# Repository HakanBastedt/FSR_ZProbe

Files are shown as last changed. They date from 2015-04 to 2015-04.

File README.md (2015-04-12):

# FSR_ZProbe
My take on FSR Z-Probe for Marlin and Repetier

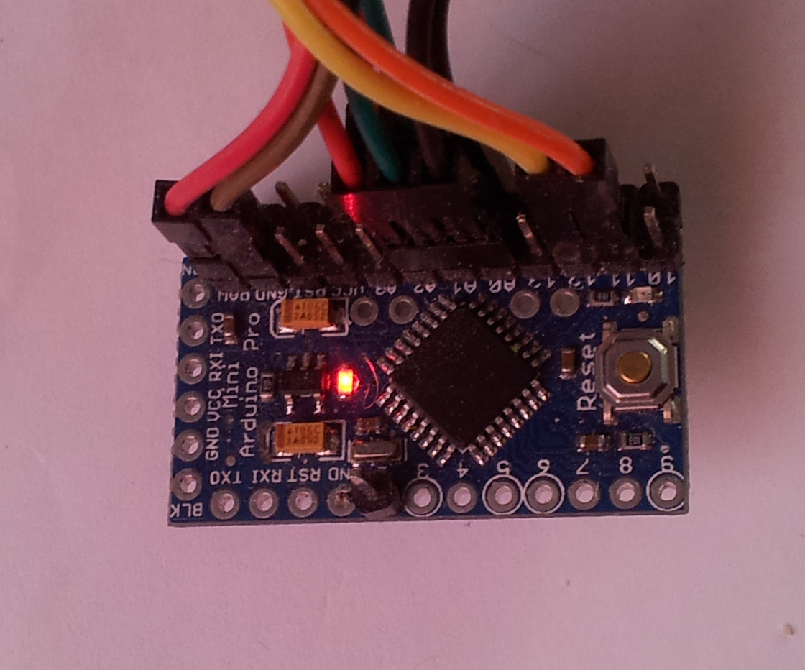
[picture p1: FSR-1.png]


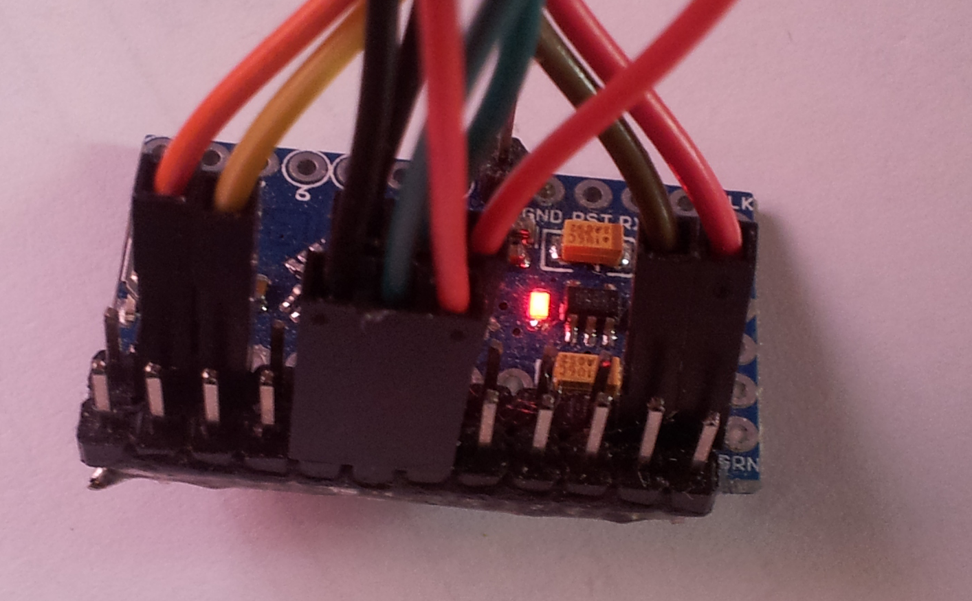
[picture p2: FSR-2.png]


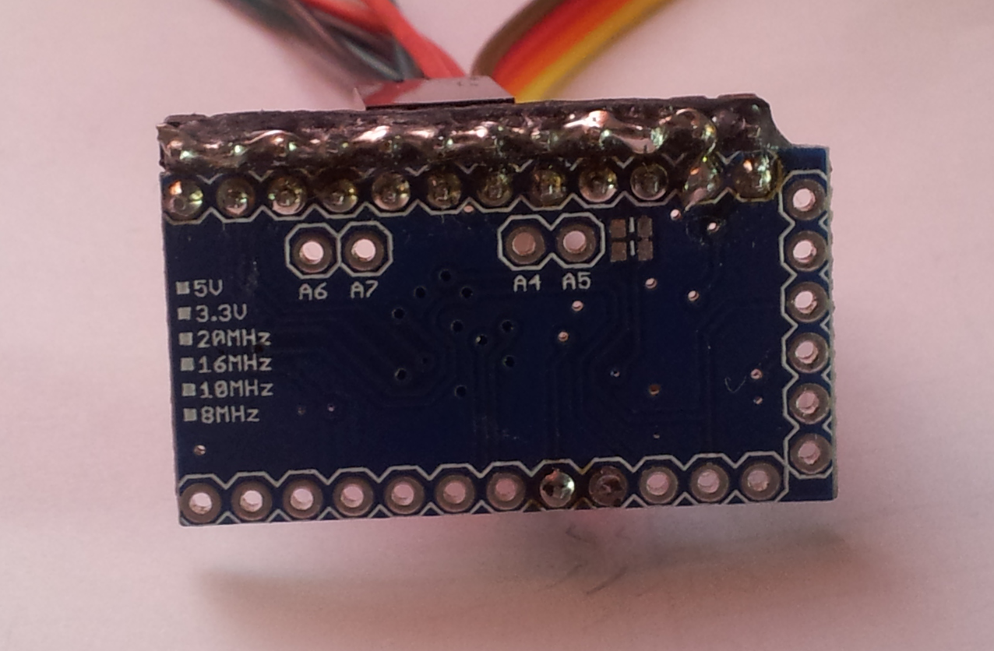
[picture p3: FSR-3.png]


For Marlin and Repetier this looks just like a
mechanical switch that gives a high voltage (+5V)
when activated and 0V when not activated (or
vice versa if you chose to).

So the output from the Arduino board goes into
Z_MIN pin on RAMPS et al.

The hardware is a Arduino Pro Mini, 5V 16 MHz,
you are on your own if you only can use 3.3V (DUE), however
I intend to make a 3.3V version for the DUE.
To program it you need the usual USB to 6-Pin serial
converter. Ebay is full of them almost for free.

I simply soldered one row of connectors and glued
one more row of connectors side by side. The pins
on the extra connector are connected to ground.

## Shopping list

* Arduino Pro Mini 5V, 16 MHz (ebay)
* USB to 6-pin serial converter (ebay). For programming the Arduino Pro Mini
* 3 x Force Sensitive Resistor FSR402 (e.g. oomlout.co.uk and other places )
* 3 x Modified Bed holders adapted to the FSRs. An stl-model is here
* You may also need to modify your heated bed glass support
* Cables and connectors
* Arduino software: fsr.ino in this repsoitory
* Repetier 0.92 with my modifications for FSR

## Details of FSR, Arduino Pro Mini and Marlin/Repetier

Due to the nature of FSR - especially the resistance
drifting problematics - one can not set a "no contact"
reference resistance when starting the printer for the day
and let it be. Due to temperature variations, small shifts in 
bed position etc a reference resistance value will drift
over time.

Therefor, just before the measurement is to be made,
a resistance reference value is defined.
The Arduino need to known when this happens,
for this a signal is used to communicate
between Marlin/Repetier and the Arduino.
On RAMPS this is the "FSR_PIN", on Arduino
this is "PIN11".

### Arduino Pro Mini pin-out

Pin | Purpose
--- | ---
D12 | Goes HIGH at contact
D13 | Goes LOW at contact
D11 | Command-pin from Marlin/Repetier
A0  | FSR input
A1  | FSR input
A2  | FSR input
A3  | FSR input (make sure N_ADC is 4)
RAW | Enough voltage to drive the Arduino Pro Mini
GND | Ground

### Commands from Marlin/Repetier to Arduino Pro Mini

Number of 1-ms pulses defines as commands. Here is the list

Puls  | Command
--- | ---
1     | Define non-contact reference resistance
2     | Use insensitive contact value next contact
3     | Show the resistance threshold value using led blinks
4-99  | Set resistance threshold value (when contact)
100   | Same as 1 (But takes shorter time to send)
101   | Same as 2

With my modifications to Marlin/Repetier these commands
can easily be given by hand with "M40 Sn", if needed. 
Should not really be needed, but you may have to adjust
the senstivity of the sensor by changing the threshold value.

Commands are sent as pulses 1ms long and 1ms pause.
A 10ms period without puls means end of sending
command and start of command execution.

There you have it.

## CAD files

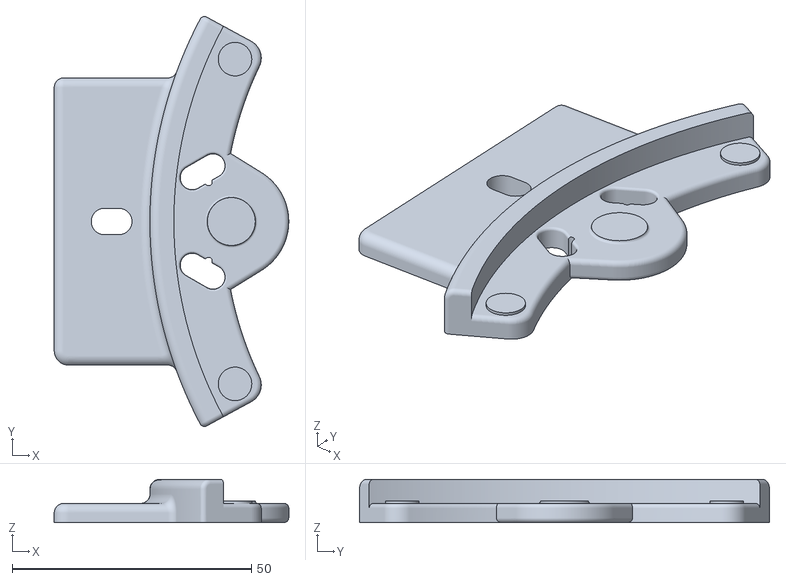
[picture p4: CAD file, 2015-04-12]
Heatbed-holder.stl
49.0 x 85.6 x 9.00

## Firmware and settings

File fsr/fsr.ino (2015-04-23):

#undef DEBUGUTSKRIFT
#define N_ADC 3
#define PIN11 11
#define EEPROM_POS 1

#include <EEPROM.h>
#include <EnableInterrupt.h>

volatile byte baseValuePulser; // Från EEPROM numera. =20;   // 20 = känslig. 70 = okänslig
#define STARTING_LIMIT 20
// 
// Att sätta baseValuePulser=25 görs med M40 S25
// 
volatile int blinkPulser; // Flagga ifall vi ska blinka inställningen
volatile byte saveEEPROM; // Flagga ifall vi ska spara till EEPROM

volatile int baseValue[N_ADC]; 
volatile int pin11Fail=false;

volatile byte inSensitiveFactor = 1;

int maxspann(int val[])  // Största spannet av ration
{
    int Max = -1;
    int Min = 30000; 
  
    for (int i=0; i < N_ADC; i++) {
      Max = Max < val[i] ? val[i] : Max;
      Min = Min > val[i] ? val[i] : Min;
    }
    return(Max-Min);
}

int minratio(int val[])  // Min value of reading
{
    int Min = 30000; 
  
    for (int i=0; i < N_ADC; i++) {
      Min = Min > val[i] ? val[i] : Min;
    }
    return(Min);
}

void readS(int read_times, int *val)
{ // Average over read_times cycles
  unsigned long ival[N_ADC];
  for (int i=0; i < N_ADC; i++)
    ival[i] = 0;  
  int n=0;
  do {
    n++;
    for (int i=0; i < N_ADC; i++)
      ival[i] += analogRead(A0+i);
  } while (n < read_times);
  for (int i=0; i < N_ADC; i++)  // Medelvärdet
    val[i] = ival[i]/n;  
}

void setBaseValue()
{
  digitalWrite(13, HIGH);    // LED on
  int val[N_ADC];
  readS(100, val); // 1000 => 0.05 seconds. 
  for (int i=0; i < N_ADC; i++)
    baseValue[i] = val[i]; 
  digitalWrite(13, LOW);
}

int touching()
{
   int ratio[N_ADC];
   int val[N_ADC];

   readS(50, val);
   for (int nadc=0; nadc < N_ADC; nadc++)  // Jobbar med ratio av baseValue
       ratio[nadc] = 100*float(val[nadc])/float(baseValue[nadc]);
   
   int spann = maxspann(ratio);  // Hur mycket skiljer det mellan största till minsta värdet
   int Min = minratio(ratio);    // Lägsta värdet.

   // Touch!
   // Limit1 väger ihop träff i mitten mot träff ovanpå en sensor.
   // 3/4*60*(spread/60*1/3+1)
   // spread = 0 => 45     Träff i mitten, alla lika
   // spread = 60 => 60    Träff i mitten
   // Detta är något jag testade fram.
   int Limit1 = inSensitiveFactor*float(100-baseValuePulser)*(1.0-float(spann)/float(100-baseValuePulser)*0.333333);
   
   // Limit två. Tar en "ren" träff. Faktorn 2.5 gäller för att komma på samma nivå som Limit1
   // En kaffekopp = ca 55 ovanpå en sensor
   // En kaffekopp = ca 42 i mitten
   int Limit2 = inSensitiveFactor*2.5*baseValuePulser;
   
#ifdef DEBUGUTSKRIFT
   // Obs att debugutskriften tar för lång tid för att köra live i Kosseln.
   // 
    Serial.print("Base= ");
    Serial.print(baseValue[0]);
    Serial.print(" ");
    Serial.print(baseValue[1]);
    Serial.print(" ");
    Serial.print(baseValue[2]);
    Serial.print(" ");
    Serial.print(val[0]);
    Serial.print(" ");
    Serial.print(val[1]);
    Serial.print(" ");
    Serial.print(val[2]);
    Serial.print(" ");
    Serial.print(ratio[0]);
    Serial.print(" ");
    Serial.print(ratio[1]);
    Serial.print(" ");
    Serial.print(ratio[2]);
    Serial.print(" ");
    Serial.print(Min);
    Serial.print(Min < Limit1 ? " < " : " > ");
    Serial.print(Limit1);
    Serial.print(Min < Limit1 ? " HIT-1 " : " . ");
    Serial.print(spann);
    Serial.print(spann > Limit2 ? " > " : " < ");
    Serial.print(Limit2);
    Serial.print(spann > Limit2 ? " HIT-2 " : " . ");
    Serial.println();
#endif

   if (Min < Limit1) {
     inSensitiveFactor=1;
     return 1;
   }
  
   if (spann > Limit2) {
     inSensitiveFactor=1;
     return 1;
   }

   return 0; // No touch
}

volatile unsigned long pulseStart11=0;
volatile unsigned long pulseStop11=0;
volatile int pulser=0;
// Tre kommandon
// 1. En puls längre än 0.2 sekunder  => setBaseValue alltså kalibrering av nollvärde
// 2. N pulser kortare 0.1 sekunder =>  setBaseValueLimit = 1-N
// 3. 100 (exakt) pulser kortare än 10 msek => setBaseValue

#define stopTimer    {TIFR1 = 0; TCNT1 = 0; TCCR1B &= ~(1 << CS10);TCCR1B &= ~(1 << CS11);TCCR1B &= ~(1 << CS12); }
#define startTimer   {TCNT1  = 0;  TIFR1  = 0;TCCR1B |= (1 << CS12);sei(); }

// Startar ca 0.2 sekunder utan aktivitet på kommandopinnen
// Ta hand om insamlad data om pulser osv
ISR(TIMER1_COMPA_vect)
{
#ifdef DEBUGUTSKRIFT
  Serial.print(" Pulser = ");
  Serial.println(pulser);
#endif

  stopTimer;
  if (pulser == 1 || pulser == 100){
    pulser = 0;
    setBaseValue();
    return; 
  }
  if (pulser == 2){
    pulser = 0;
    inSensitiveFactor=3;
    return; 
  }
  if (pulser == 3 || pulser == 101){
    pulser = 0;
    blinkPulser=baseValuePulser; 
    return; 
  }
  if (pulser > 1) {
      baseValuePulser = pulser;
      saveEEPROM=true;
  }
  pulser = 0;
}

// ISR för input på kommandopinnen pinne-11
void pin11()
{
  if (digitalRead(PIN11)) {  // UP
    pulseStart11 = micros();
  } else {  // DOWN - completing the pulse
    pulseStop11 = micros();
 
    if (pulseStop11 - pulseStart11 < 10000) { // Kommando 2,3. Pulser kortare än 0.1 sekund
      pulser++;
      startTimer;             // Reload
    } else {                  // Fail. reset
      pulseStop11 = pulseStart11 = 0; // Reset
      pulser = 0;
      pin11Fail = true;
    }
  }    
}

void setup() 
{
    for (int i=0; i < N_ADC; i++) {
        pinMode(A0+i, INPUT);      // For ADC
        digitalWrite(A0+i, HIGH);  // Enable internal pullups
     }
    setBaseValue();                // Initial
    baseValuePulser = EEPROM.read(EEPROM_POS);  // Orka ställa in varje gång. Nä...
    if (baseValuePulser < STARTING_LIMIT/2 || baseValuePulser > 100) {
      baseValuePulser = STARTING_LIMIT;
      EEPROM.write(EEPROM_POS, baseValuePulser); // För första gången är tanken. Korrigerar kasst värde
    } 
    
    pinMode(PIN11, INPUT);         // Kommandopinnen
    digitalWrite(PIN11, HIGH);
    enableInterrupt(11, &pin11, CHANGE); // M40 S0

    cli();                         // Initiera timern
    TCCR1A = 0;
    TCCR1B = 0;
    TCNT1  = 0;
    TIMSK1  |= (1 << OCIE1A);      
    OCR1A = 625;                   // Set compare match register for 100 Hz increments
    TCCR1B  |= (1 << WGM12);       // Turn on CTC mode
    sei();
  
    pinMode(12, OUTPUT);           // Output to RAMPS
    digitalWrite(12, HIGH);        // Off
    
    pinMode(13, OUTPUT);           // LED pin
    digitalWrite(13, LOW);         // Inverted output to RAMPS

    blinkPulser=EEPROM.read(EEPROM_POS);
    saveEEPROM=false;

#ifdef DEBUGUTSKRIFT
    Serial.begin(115200);
#endif
}

void loop() 
{
    if (touching()) {
        digitalWrite(12, LOW);
        digitalWrite(13, HIGH);
    } else {
        digitalWrite(12, HIGH);      
        digitalWrite(13, LOW);
    }
    if (blinkPulser > 0) {
      digitalWrite(13, LOW);
      delay(1000);
      for (; blinkPulser >= 10; blinkPulser = blinkPulser - 10) {
        digitalWrite(13, HIGH);
        delay(1000);
        digitalWrite(13, LOW);
        delay(1000);
      }
      while(blinkPulser-- > 0) {
        digitalWrite(13, HIGH);
        delay(300);
        digitalWrite(13, LOW);
        delay(300);
      }
      delay(300);
      blinkPulser=0;
    }
    if (saveEEPROM) {
      EEPROM.write(EEPROM_POS, baseValuePulser); // Spara tills nästa gång
      for (int  i=0; i < 3; i++) {
        digitalWrite(13,HIGH);
        delay(50);
        digitalWrite(13,LOW);
        delay(50);
      }
      saveEEPROM=false;
    }
    if (pin11Fail) {
      for (int  i=0; i < 10; i++) {
        digitalWrite(13,HIGH);
        delay(50);
        digitalWrite(13,LOW);
        delay(50);
      }
      pin11Fail = false;
    }
}

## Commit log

2015-04-12 Added stl-file for heatbed-holder
    [Heatbed-holder.stl]
2015-04-23 Works with 8 MHz, 3.3V as well. Moved to EnableInterrupt library
